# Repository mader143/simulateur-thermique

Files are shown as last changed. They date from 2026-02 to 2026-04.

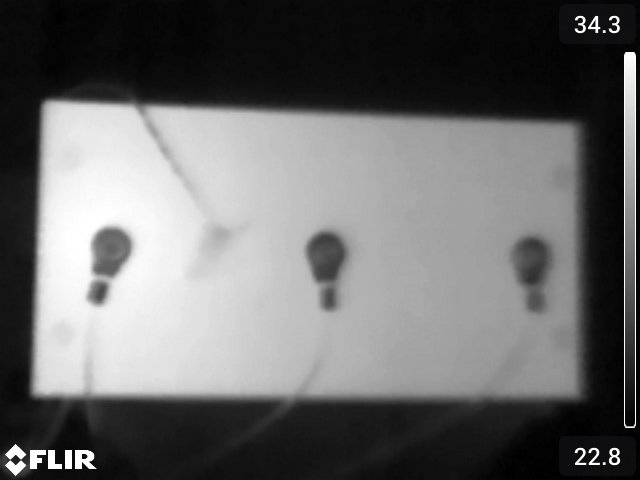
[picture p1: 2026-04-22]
PhotosThermiques_ValidationProto/FLIR0060.jpg

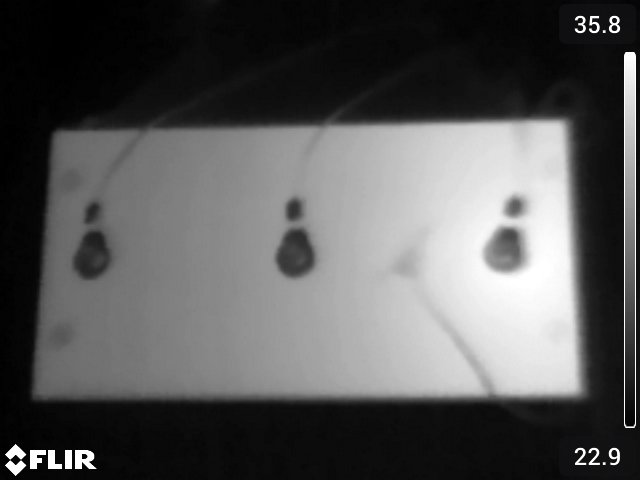
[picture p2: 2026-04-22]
PhotosThermiques_ValidationProto/FLIR0058.jpg

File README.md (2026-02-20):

# Simulateur Thermique
# Équipe 5 (Da best)

## Description

Simulateur thermique 2D pour modéliser la diffusion de chaleur dans une plaque métallique. Le projet regroupe une simulation numérique en Python avec interface graphique PyQt5, une simulation du système et du régulateur via Simulink (Matlab), du code Arduino pour l'acquisition et la régulation d'un prototype réel, et les données expérimentales pour la validation des différents paramètres identifiés.

## Contenu du projet

**Simulation Python** : Résolution par différences finies de l'équation de diffusion thermique, interface utilisateur interactive, génération de résultats et animations.

**Simulation Simulink** : Division du système/procédé en sous-systèmes et identification des fonctions de transfert de ceux-ci. Ajout d'un régulateur PID pour valider la commande contrôlant le prototype.

**Code Arduino** : Contrôleur PID pour régulation thermique, conditionnement des signaux, identification expérimentale, enregistrement des données.

**Conception PCB** : Schémas et circuits imprimés KiCad avec Arduino Mega 2560, amplificateurs opérationnels, et conditionnement analogique pour la lecture de la température en trois points sur la plaque métallique.

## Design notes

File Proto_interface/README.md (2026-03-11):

IMPORTANT **NE PAS CHANGER LES NOMS DES FICHIERS DANS Proto_Interface**

Pour pouvoir contrôler le Arduino par vscode :
1. Installer l'extension PlatformIO IDE
2. Appuyer sur la tête d'extraterrestre à gauche
3. Appuyer sur 'Project and configuration'
4. Dans 'simulateur-thermique\Proto_interface', appuyer sur 'Open'
5. Proto_interface ouvrira une seconde fois au même niveau que simulateur-thermique. C'est celui-là qui permet de rouler le code Arduino.

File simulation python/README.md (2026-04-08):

# Simulateur de diffusion de la chaleur

Simulation numérique 2D de la diffusion thermique dans une plaque rectangulaire avec interface graphique.

---

## Avant de commencer

Il faut avoir **Python 3.8 ou plus** installé sur l'ordinateur.

Ensuite, il faut installer les packages nécessaires en ouvrant un terminal et en collant cette commande :

```bash
pip install numpy numba PyQt5 pyqtgraph matplotlib
```

---

## Lancer le simulateur

S'assurer que tous les fichiers du projet sont dans le **même dossier**, puis exécuter :

```bash
python main.py
```

Mettre la fenêtre en plein écran pour voir tous les graphiques.

---

## Utilisation rapide

1. Cliquer sur **Charger les paramètres (json)** pour charger les valeurs par défaut.
2. Ajuster les paramètres ou les positions des thermistances si nécessaire.
3. Cliquer sur **Lancer la simulation** *(quelques secondes de délai normal au premier lancement)*.
4. Une fois terminé, choisir un dossier, entrer un nom de fichier, et cliquer sur **Sauvegarder les résultats**.

Voir le Manuel d'utilisation (.pdf) pour plus de détails.

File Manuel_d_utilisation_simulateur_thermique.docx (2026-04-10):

MANUEL D’UTILISATION - SIMULATEUR DE LA CHALEUR

1. Ouvrir le fichier nommé main.py et exécuter (run) le code.

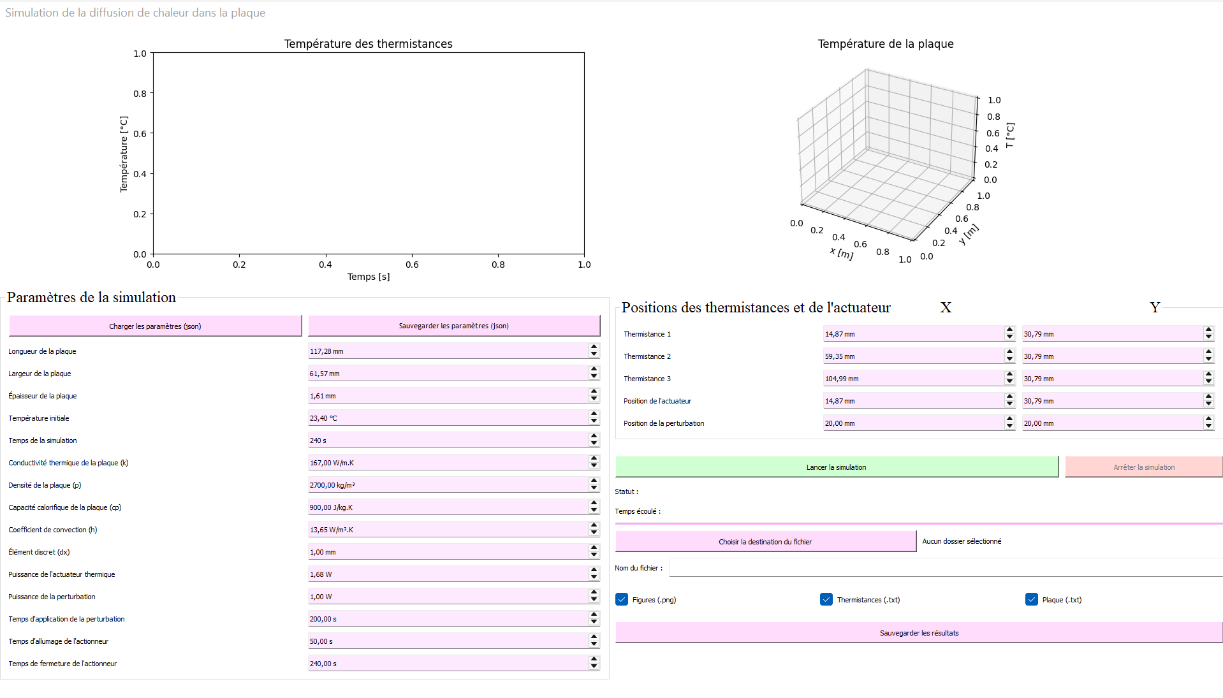
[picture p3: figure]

2. La fenêtre de l’interface s’ouvre. Mettre en grand écran pour voir tous les graphiques et fonctionnalités disponibles.
3. Pour débuter une simulation, choisir ou charger les paramètres de la simulation dans les champs de texte. Pour charger les paramètres par défaut contenus dans le fichier params_sim.json, il suffit de cliquer sur le bouton Charger les paramètres (json).
4. Il est également possible de modifier l’emplacement des thermistances, de l’actuateur et de la perturbation dans la section Position des thermistances et de l’actuateur.
5. Cliquer sur Lancer la simulation. Il est normal que cela prenne quelques secondes avant de démarrer lors de la première exécution de la simulation.
6. Une fois que le statut de la simulation est Simulation terminée, il est possible de sauvegarder les figures ainsi que les données utilisées pour les générer (.txt) en choisissant la destination sur l’ordinateur, en spécifiant le nom du fichier et en cliquant sur Sauvegarder les fichiers.

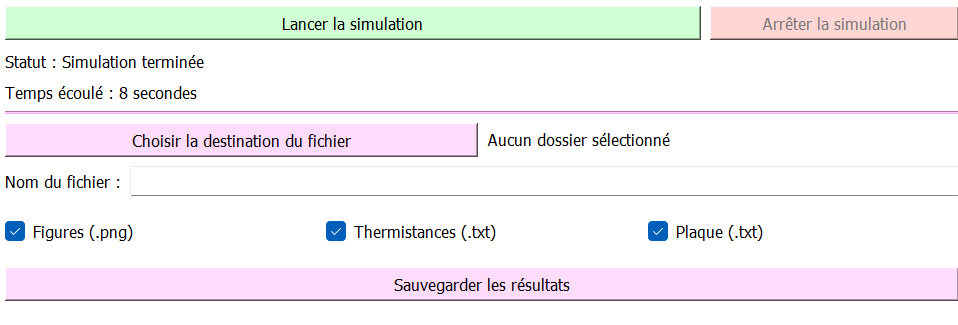
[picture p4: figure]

7. Le bouton Arrêter la simulation permet de arrêter la simulation. Il est également possible de sauvegarder les fichiers dans ce cas. Il n’est pas possible de continuer la simulation arrêter.

MANUEL D’UTILISATION - SIMULATEUR SIMULINK

1. Les fichiers nécessaires au bon fonctionnement du simulateur sont :
  a. simulink_08_04_procede.slx
  b. logique.m
  c. variables_simulation.m
  d. boucle_fermee.png
  e. boucle_ouverte.png
2. Une fois que le fichier simulink_08_04_procede.slx est ouvert, il faut run (exécuter) les fichiers logique.m et variables_simulation.m (à partir de la fenêtre classroom use).

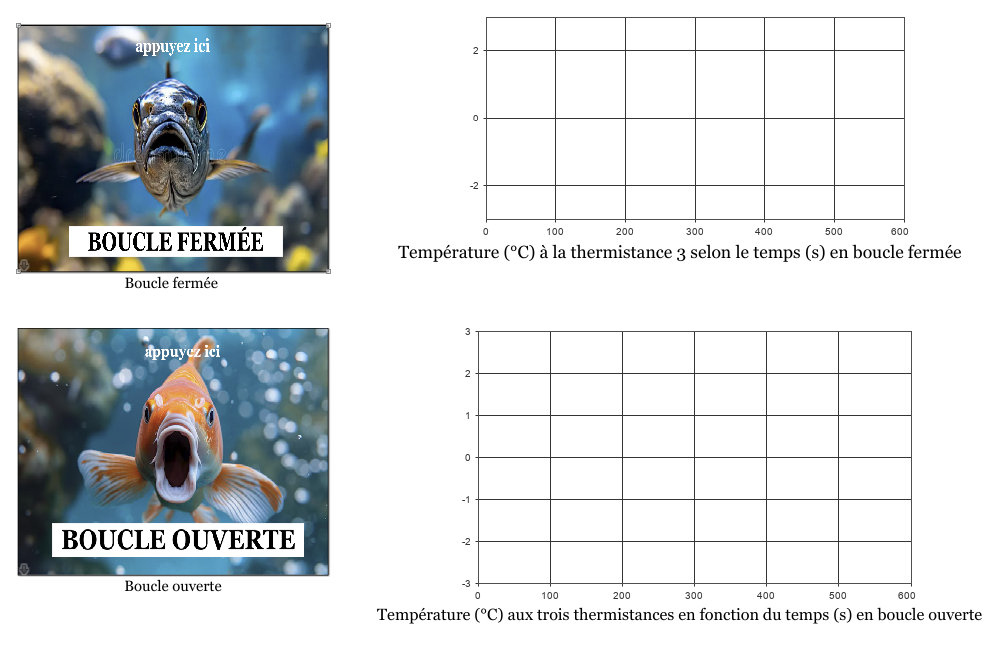
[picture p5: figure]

3. En cliquant sur l’autre fenêtre, l’interface s’affiche. Il est composé de 4 éléments : les paramètres de simulation en boucle ouverte et en boucle fermée et les graphiques affichant la réponse en boucle ouverte et en boucle fermée. Il ressemble à :

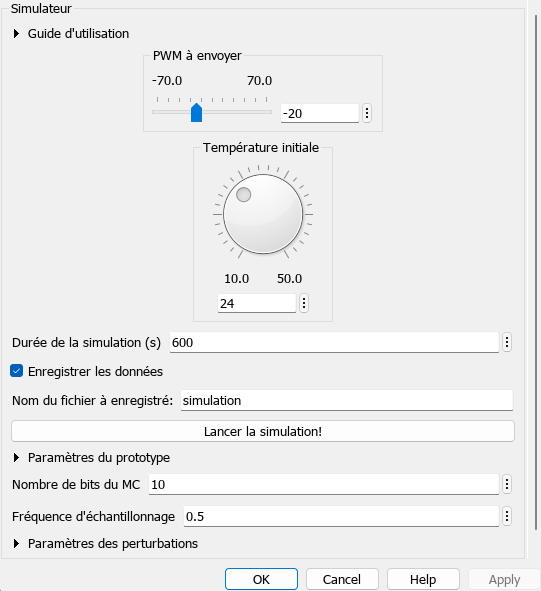
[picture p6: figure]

4. Pour la boucle ouverte, double cliquez sur le poisson ayant la bouche ouverte. Il est alors possible de spécifier l’échelon de commande voulu (PWM), la température initiale (°C), certains paramètres du prototype et les paramètres des perturbations.

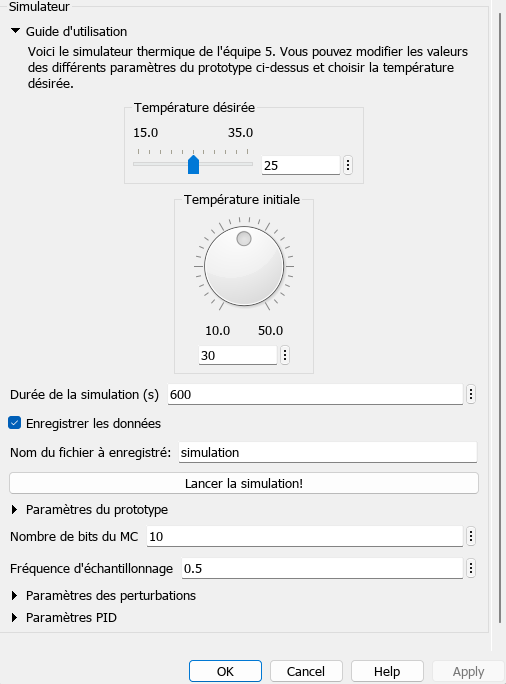
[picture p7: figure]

5. Pour la boucle fermée, de la même façon, choisir la température intitiale et désirée. D’autres paramètres modifiables sont aussi disponibles.
6. Les modifications des différentes fonctions de transfert et la visualisation des signaux se font directement dans la simulation (blocs et sous-systèmes). Cliquez sur la flèche dans le coin inférieur gauche de l’image correspondante à la boucle désirée pour y accéder.

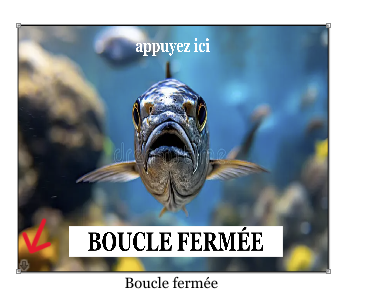
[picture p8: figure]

Exemple pour la boucle fermée :

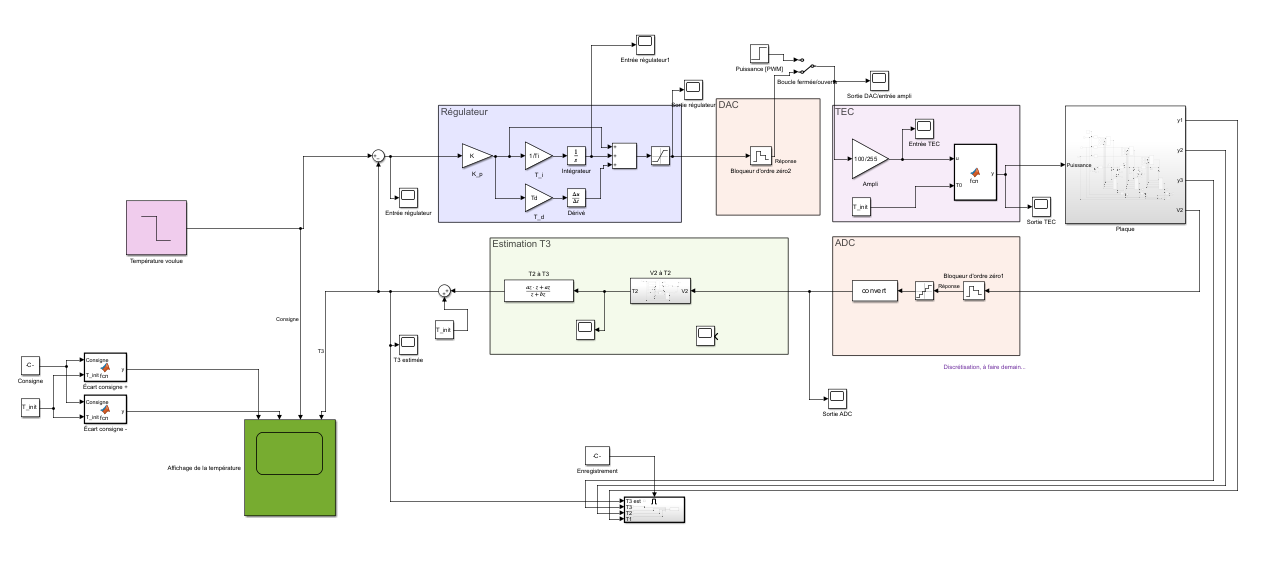
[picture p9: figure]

Équipe 05 GPH-2104 (H26)

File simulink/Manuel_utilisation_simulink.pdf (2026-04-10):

Équipe 05 | GPH-2104 (H26)
| MANUEL D’UTILISATION - SIMULATEUR SIMULINK

### 1. Les fichiers nécessaires au bon fonctionnement du simulateur sont :

a. simulink_08_04_procede.slx
b. logique.m
c. variables_simulation.m
d. boucle_fermee.png
e. boucle_ouverte.png
2. Une fois que le fichier simulink_08_04_procede.slx est ouvert, il faut run (exécuter) les fichiers logique.m et variables_simulation.m (à partir de la fenêtre classroom use).
3. En cliquant sur l’autre fenêtre, l’interface s’affiche. Il est composé de 4 éléments : les paramètres de simulation en boucle ouverte et en boucle fermée et les graphiques affichant la réponse en boucle ouverte et en boucle fermée. Il ressemble à :

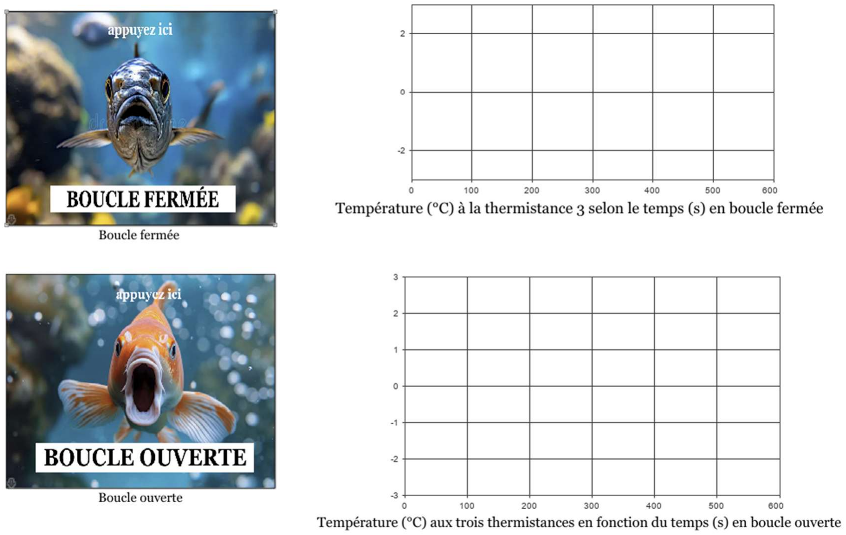
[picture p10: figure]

4. Pour la boucle ouverte, double cliquez sur le poisson ayant la bouche ouverte. Il est alors possible de spécifier l’échelon de commande voulu (PWM), la température initiale (°C), certains paramètres du prototype et les paramètres des perturbations.

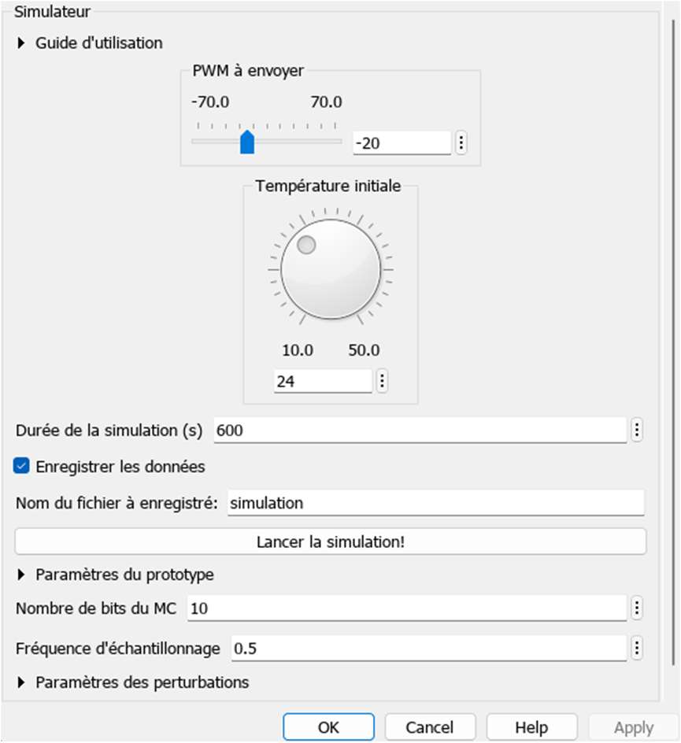
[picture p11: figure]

5. Pour la boucle fermée, de la même façon, choisir la température intitiale et désirée. D’autres paramètres modifiables sont aussi disponibles.

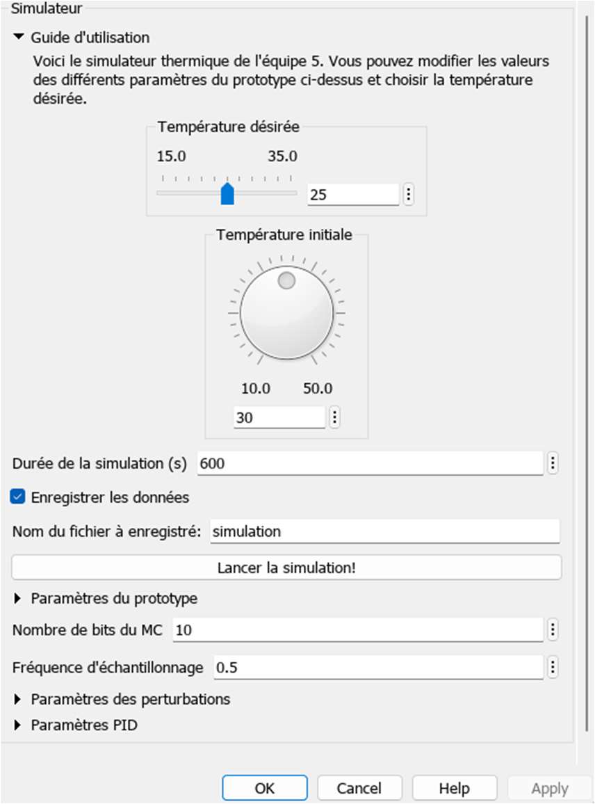
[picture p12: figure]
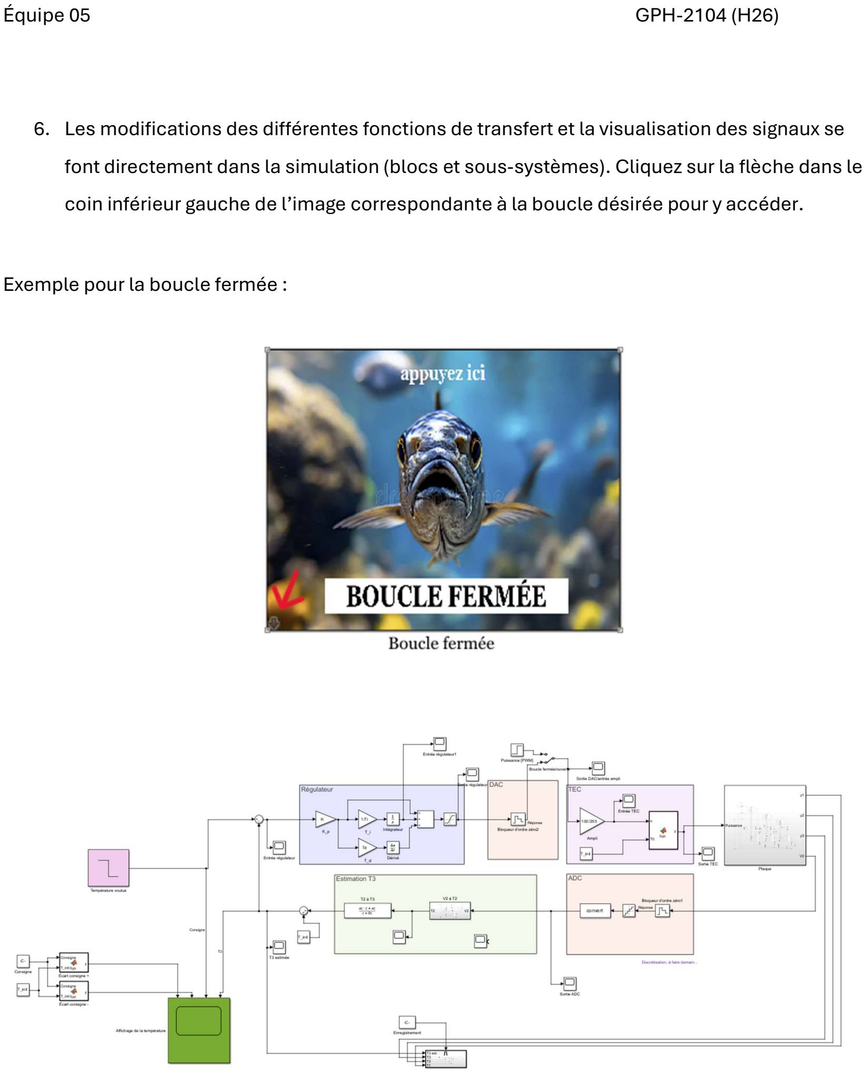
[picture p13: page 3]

6. Les modifications des différentes fonctions de transfert et la visualisation des signaux se font directement dans la simulation (blocs et sous-systèmes). Cliquez sur la flèche dans le coin inférieur gauche de l’image correspondante à la boucle désirée pour y accéder.

Exemple pour la boucle fermée :

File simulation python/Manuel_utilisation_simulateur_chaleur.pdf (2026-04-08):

Équipe 05 | GPH-2104 (H26)
| MANUEL D’UTILISATION - SIMULATEUR DE LA CHALEUR
1. Ouvrir le fichier nommé main.py et exécuter (run) le code.
2. La fenêtre de l’interface s’ouvre. Mettre en grand écran pour voir tous les graphiques et fonctionnalités disponibles.

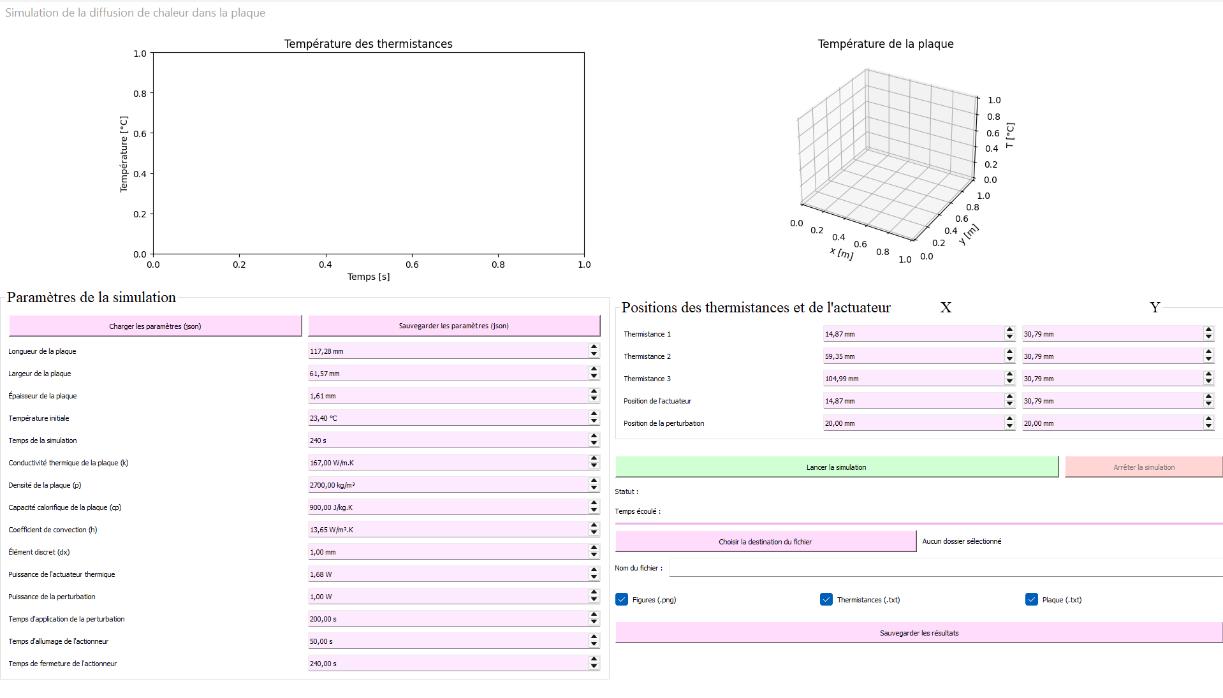
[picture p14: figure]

3. Pour débuter une simulation, choisir ou charger les paramètres de la simulation dans les champs de texte. Pour charger les paramètres par défaut contenus dans le fichier params_sim.json, il suffit de cliquer sur le bouton Charger les paramètres (json).

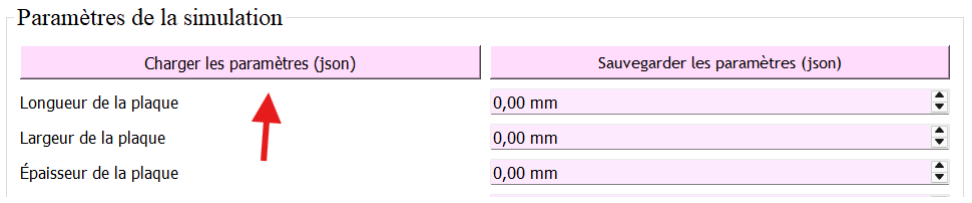
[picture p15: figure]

4. Il est également possible de modifier l’emplacement des thermistances, de l’actuateur et de la perturbation dans la section Position des thermistances et de l’actuateur.
5. Cliquer sur Lancer la simulation. Il est normal que cela prenne quelques secondes avant de démarrer lors de la première exécution de la simulation.

Équipe 05 | GPH-2104 (H26)
6. Une fois que le statut de la simulation est Simulation terminée, il est possible de sauvegarder les figures ainsi que les données utilisées pour les générer (.txt) en choisissant la destination sur l’ordinateur, en spécifiant le nom du fichier et en cliquant sur Sauvegarder les fichiers.

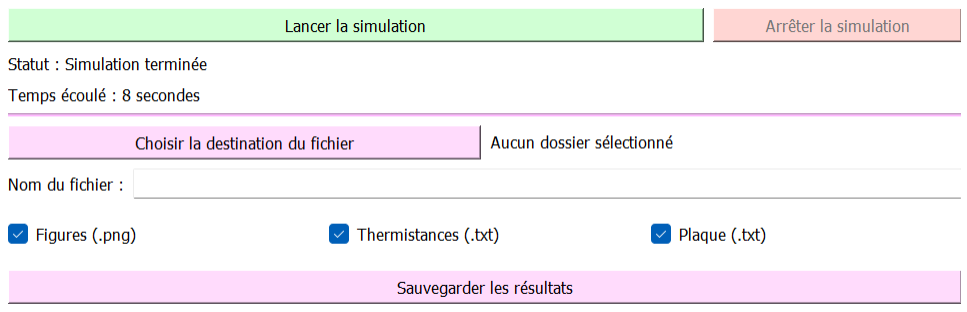
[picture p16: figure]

7. Le bouton Arrêter la simulation permet de arrêter la simulation. Il est également possible de sauvegarder les fichiers dans ce cas. Il n’est pas possible de continuer la simulation arrêter.

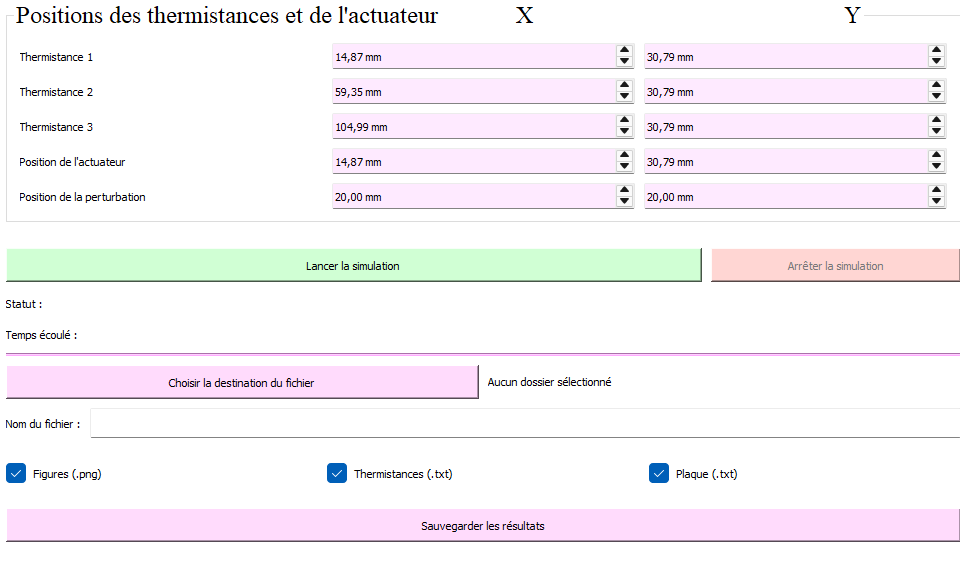
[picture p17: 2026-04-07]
simulation python/Screenshot rapport/Interface_simul_python_position_therm.png

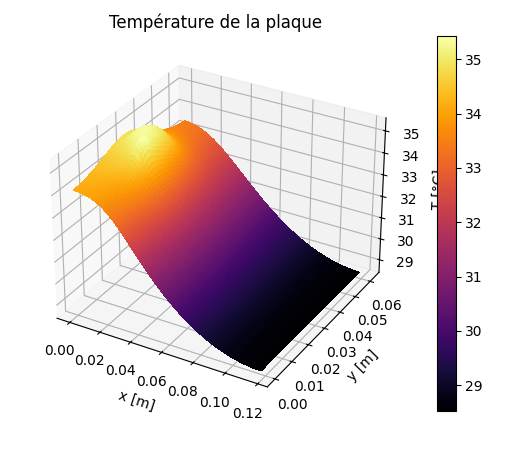
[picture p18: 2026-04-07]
simulation python/Screenshot rapport/Interface_simul_python_plaque.png

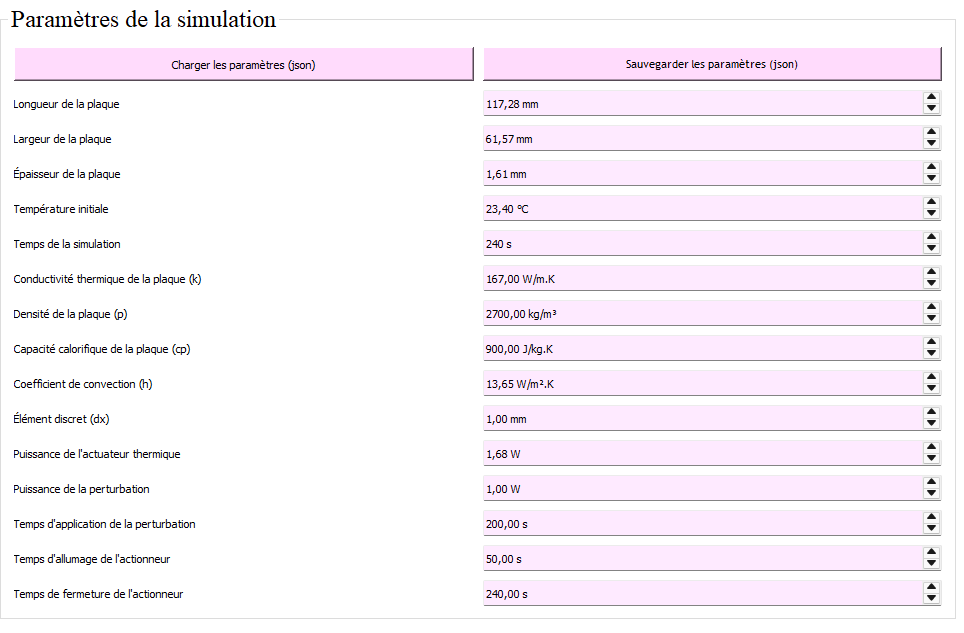
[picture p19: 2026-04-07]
simulation python/Screenshot rapport/Interface_simul_python_parametres.png

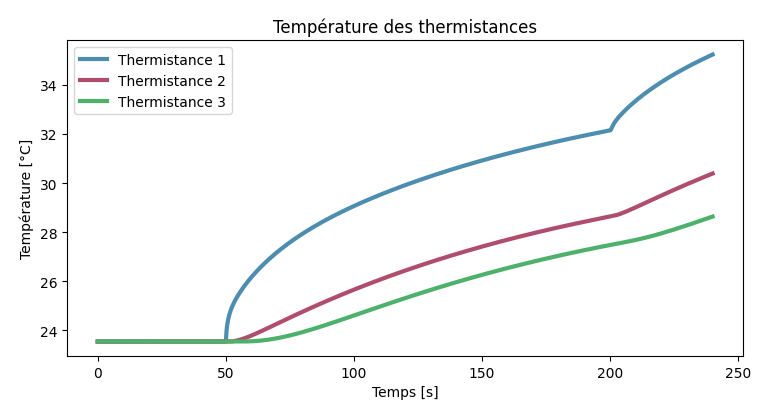
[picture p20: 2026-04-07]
simulation python/Screenshot rapport/Interface_simul_python_graphique_temps.png

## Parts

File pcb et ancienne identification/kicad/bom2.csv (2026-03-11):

Id | Référence | Empreinte | Quantité | Désignation | Fournisseur et réf
1 | RV3,RV2,RV4,RV1 | trimpot | 4 | R_Potentiometer_Trim
2 | J1 | MTA_CONN2_640445-2 | 1 | MTA_02
3 | R6,R4,R11,R1 | Resistance SMT | 4 | 10K
4 | R3,R10,R14,R9,R5,R19,R7,R12 | Resistance SMT | 8 | 5.6K
5 | C1,C4,C2,C3 | condensateur 1uF | 4 | 1 μF
6 | TH3,TH2,TH4,TH1 | MTA_CONN2_640445-2 | 4 | Screw_Terminal_01x02
7 | D1 | LED_D5.0mm | 1 | LED
8 | U1,U3,U2,U4 | LMC6482_SMT | 4 | LMC6482IMX_NOPB
9 | R8,R2,R13,R15 | Resistance SMT | 4 | 3.3K
10 | R18 | Resistance SMT | 1 | 560
11 | J2 | MTA_CONN4_640445-4 | 1 | MTA_04
12 | power2,analogA0-A7,comm1,analogA8-A15,pwm2 | PinHeader_1x08_P2.54mm_Vertical | 5 | Conn_01x08_Pin
13 | pwm1 | PinHeader_1x10_P2.54mm_Vertical | 1 | Conn_01x10_Pin

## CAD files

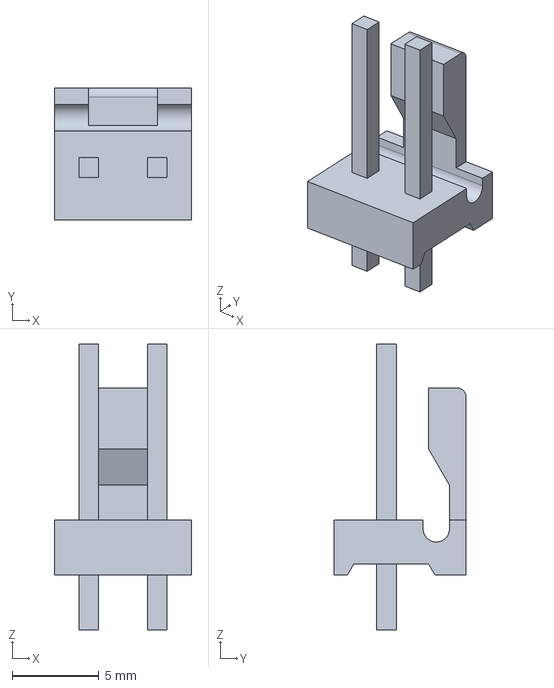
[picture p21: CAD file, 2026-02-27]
pcb et ancienne identification/kicad/CON_02_MTA_MALE_MATHILDE/c-640445-2-al-3d.stp
7.92 x 7.62 x 16.5 mm

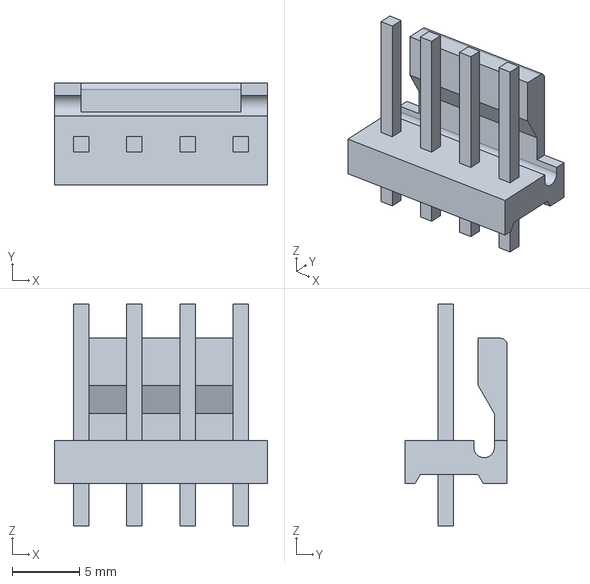
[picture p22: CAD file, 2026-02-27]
pcb et ancienne identification/kicad/CON_04_MTA_MALE_MATHILDE/c-640445-4-al-3d.stp
15.8 x 7.62 x 16.5 mm

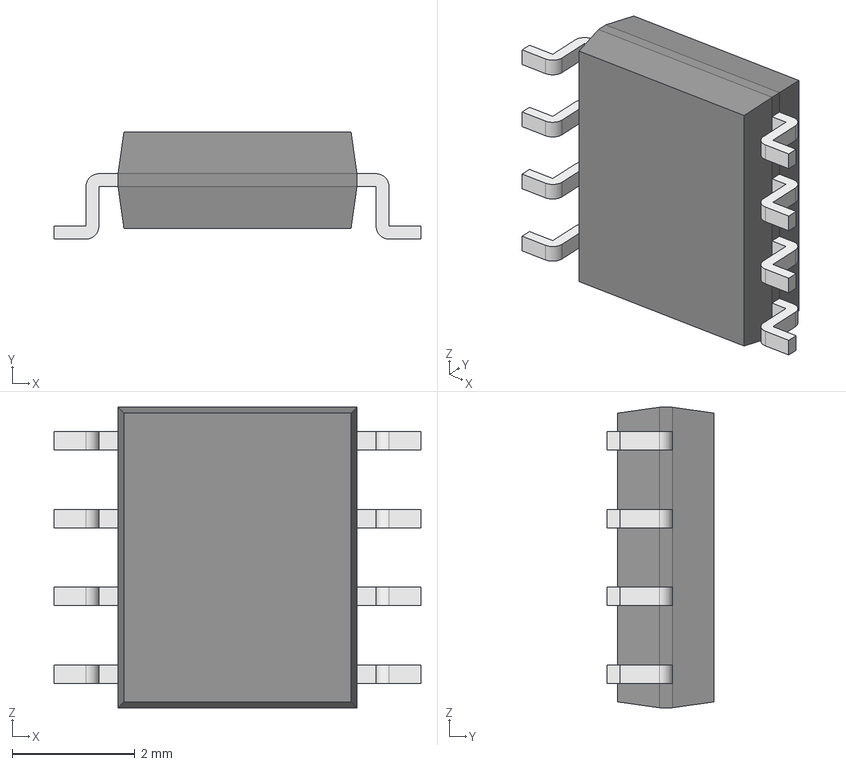
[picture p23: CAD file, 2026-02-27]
pcb et ancienne identification/kicad/LMC6482_SMT_MATHILDE/LMC6482IMX_NOPB.step
5.99 x 1.75 x 4.91 mm
Body001 (Mirror #1) x 4
XY-plane x 12
X-axis x 12

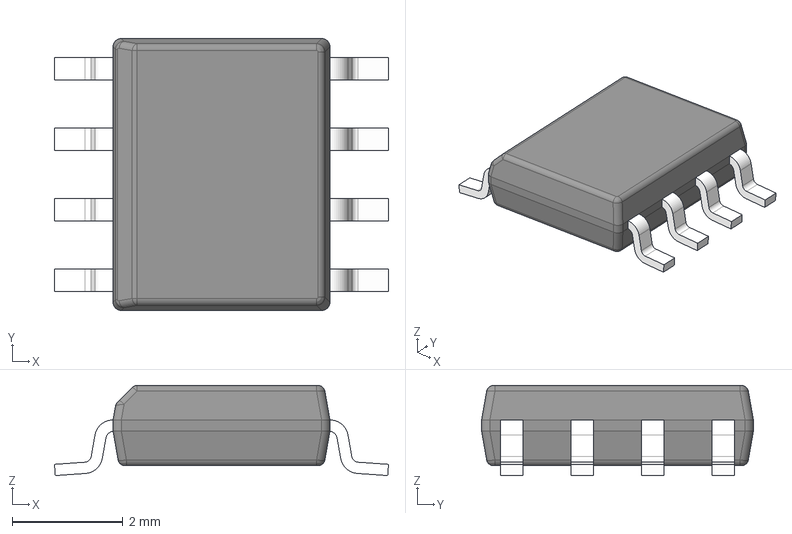
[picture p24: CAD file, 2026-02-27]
pcb et ancienne identification/kicad/LMC6482_SMT_MATHILDE/D0008A.stp
6.02 x 4.90 x 1.63 mm
BODY-SO
LEAD-D0008A x 8

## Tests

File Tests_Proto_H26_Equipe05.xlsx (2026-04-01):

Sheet: Plan de Test
Déroulement général
 | Un membre de l'équipe enseignante démarre l'exécution du plan de test, il effectue les tests de convivialité et note les résultats dans son propre fichier excel
 | Le test sans perturbation est ensuite démarré. Au bout d'une minute ou deux, le membre de l'équipe enseignante prend en photo les courbes affichées, en prenant soin d'avoir le numéro de l'équipe dans la photo.
 | Le membre de l'équipe enseignante peut alors quitter
 | L'équipe complète le test selon les directives ci-bas et sauve les données pour remplir l'onglet "Réponse à l'échelon"
 | Lorsque prête pour le test de perturbation, l'équipe lève la main
 | Un membre de l'équipe enseignante démarre le test, lorsque la perturbation est allumée, il prend les courbes affichées en photo, avec le numéro d'équipe et peut quitter
 | L'équipe complète le test selon les directives ci-bas et sauve les données pour remplir l'onglet "Réponse perturbation"
 | Lorsque prête pour le test de robutesse, l'équipe lève la main
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

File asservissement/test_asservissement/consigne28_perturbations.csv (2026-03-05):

temps_s | temperature_C | erreur | commande_u
0.000 | 23.17 | 4.83 | 42.34
0.500 | 23.17 | 4.83 | 43.16
1.000 | 23.23 | 4.77 | 43.43
1.500 | 23.30 | 4.70 | 43.68
2.000 | 23.36 | 4.64 | 43.93
2.500 | 23.36 | 4.64 | 44.72
3.000 | 23.42 | 4.58 | 44.96
3.500 | 23.48 | 4.52 | 45.18
4.000 | 23.48 | 4.52 | 45.95
4.500 | 23.55 | 4.45 | 46.17
5.000 | 23.55 | 4.45 | 46.93
5.500 | 23.67 | 4.33 | 46.58
6.000 | 23.74 | 4.26 | 46.77
6.500 | 23.80 | 4.20 | 46.94
7.000 | 23.86 | 4.14 | 47.10
7.500 | 23.92 | 4.08 | 47.26
8.000 | 23.99 | 4.01 | 47.40
8.500 | 24.05 | 3.95 | 47.53
9.000 | 24.11 | 3.89 | 47.66
9.500 | 24.24 | 3.76 | 47.22
10.000 | 24.30 | 3.70 | 47.31
10.500 | 24.43 | 3.57 | 46.85
11.000 | 24.49 | 3.51 | 46.91
11.500 | 24.61 | 3.39 | 46.41
12.000 | 24.74 | 3.26 | 45.89
12.500 | 24.86 | 3.14 | 45.35
13.000 | 24.92 | 3.08 | 45.34
13.500 | 25.05 | 2.95 | 44.77
14.001 | 25.17 | 2.83 | 44.18
14.501 | 25.30 | 2.70 | 43.57
15.001 | 25.42 | 2.58 | 42.94
15.501 | 25.55 | 2.45 | 42.29
16.001 | 25.67 | 2.33 | 41.62
16.501 | 25.73 | 2.27 | 41.47
17.001 | 25.92 | 2.08 | 40.23
17.501 | 26.04 | 1.96 | 39.50
18.001 | 26.17 | 1.83 | 38.75
18.501 | 26.29 | 1.71 | 37.97
19.001 | 26.41 | 1.59 | 37.18
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

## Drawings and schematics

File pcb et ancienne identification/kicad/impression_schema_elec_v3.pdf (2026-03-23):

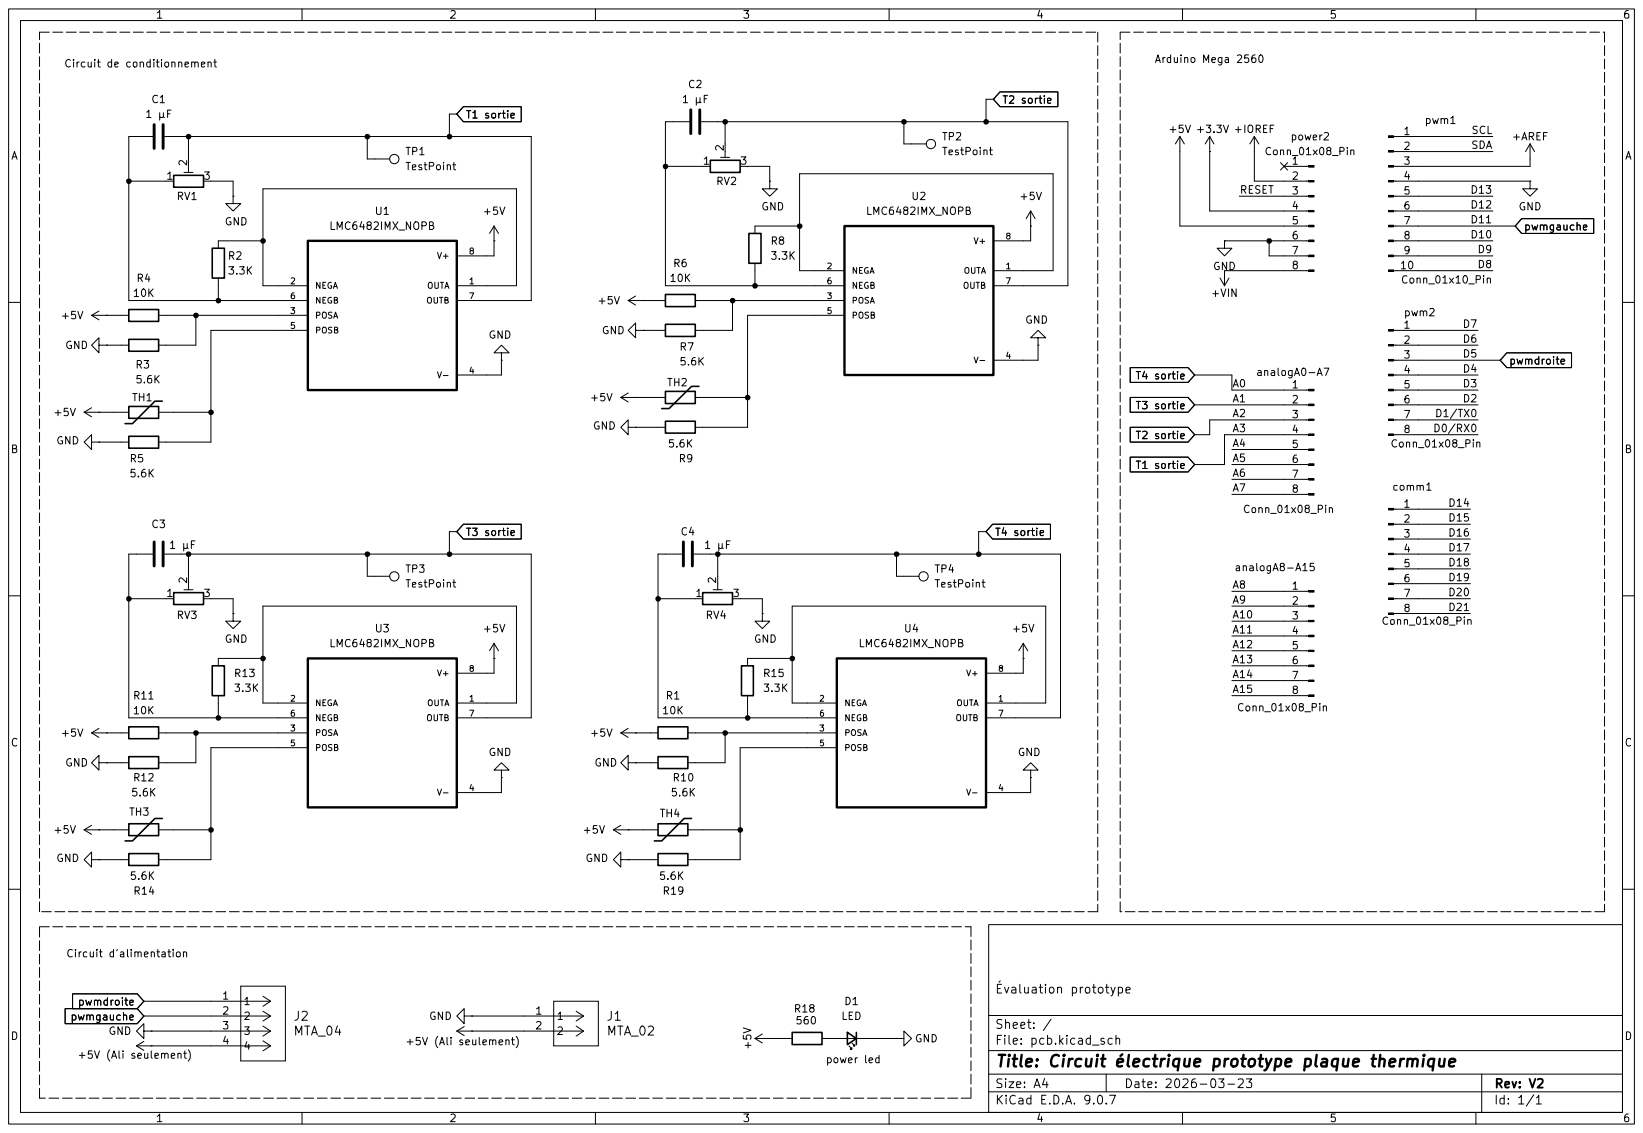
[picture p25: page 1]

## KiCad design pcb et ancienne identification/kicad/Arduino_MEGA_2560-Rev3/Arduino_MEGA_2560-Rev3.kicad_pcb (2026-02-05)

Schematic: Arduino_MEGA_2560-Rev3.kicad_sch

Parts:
ADCH31: 8x1F-H8.5; SMARTPRJ_1X08
ADCL31: 8x1F-H8.5; SMARTPRJ_1X08
C1, C14, C15: 22p; SMARTPRJ_C0603-ROUND
C2, C3, C4, C5, C6, C7, C8, C9, C11, C12: 100n; SMARTPRJ_C0603-ROUND
C10, C13: 1u; SMARTPRJ_C0603-ROUND
COMMUNICATION31: 8x1F-H8.5; SMARTPRJ_1X08
D1: M7; DIODE_SMB
D2, D3: CD1206-S01575; DIODE_MINIMELF
F1: MF-MSMF050-2 500mA; RCL_L1812
FD1, FD2, FD3, FD4: FIDUCIALMOUNT; SMARTPRJ_FIDUCIA-MOUNT
GROUND31: JUMPER_SJ
IC1: NCP1117ST50T3G; LINEAR_SOT223
IC3: ATMEGA2560-16AU; SMARTPRJ_TQFP100
IC4: ATMEGA16U2-MU; SMARTPRJ_MLF32
IC6: LP2985-33DBVR; SMARTPRJ_SOT23-DBV
IC7: LMV358IDGKR; LINEAR_MSOP08
ICSP1_31: 3x2M; SMARTPRJ_2X03
ICSP_31: 3x2M; SMARTPRJ_2X03
JP5: 2x2M - NM; SMARTPRJ_2X02
JP6: 10x1F-H8.5; SMARTPRJ_1X10
L1: BLM21; WUERTH-ELEKTRONIK_0805
L31: YELLOW; LED_CHIP-LED0805
ON31: GREEN; LED_CHIP-LED0805
PC1, PC2: 47u; RCL_PANASONIC_D
POWER31: 8x1F-H8.5; SMARTPRJ_1X08
PWML31: 8x1F-H8.5; SMARTPRJ_1X08
R1, R2: 1M; SMARTPRJ_R0603-ROUND
RESET31: TS42031-160R-TR-7260; SMARTPRJ_TS42
RESET-EN31: JUMPER_SJ
RN1, RN5: 10K; RESISTOR-DIL_CAT16
RN2: 22R; RESISTOR-DIL_CAY16
RN3, RN4: 1k; RESISTOR-DIL_CAY16
RX31: YELLOW; LED_CHIP-LED0805
T1: FDN340P; ZETEX_SOT-23
TX31: YELLOW; LED_CHIP-LED0805
U$1: DISCLAIMER; SMARTPRJ_DISCLAIMER
X1: POWERSUPPLY_DC21MMX; SMARTPRJ_POWERSUPPLY_DC-21MM
X2: USB-B_TH; SMARTPRJ_PN61729
XIO31: 18x2F-H8.5; SMARTPRJ_2X18
Y1: CSTCE16M0V53-R0 16MHZ; SMARTPRJ_RESONATOR
Y2: 16MHz; SMARTPRJ_QS
Z1, Z2: CG0603MLC-05E; VARISTOR_CT_CN0603

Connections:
+3V3: C13.2, IC6.5 (OUT), IC7.6 (-IN), POWER31.4
+5V: C4.1, C5.1, C6.1, C9.1, C11.2, D2.C, D3.C, IC1.2 (OUT), IC1.4 (OUT), IC3.10 (VCC), IC3.31 (VCC1), IC3.61 (VCC2), IC3.80 (VCC3), IC3.100 (AVCC), IC4.4 (VCC), IC4.32 (AVCC), IC6.1 (IN), IC6.3 (ON/~OFF), IC7.8 (V+), ICSP1_31.2, ICSP_31.2, PC2.+, POWER31.2, POWER31.5, RN1.6 (2), RN1.7 (2), RN3.1, RN4.5 (2), RN4.6 (2), RN5.2 (1), RN5.8 (2), T1.2 (S), XIO31.1, XIO31.2
/8PB4: IC4.18 ((T1/PCINT4)PB4), JP5.1
/8PB5: IC4.19 ((PCINT5)PB5), JP5.3
/8PB6: IC4.20 ((PCINT6)PB6), JP5.2
/8PB7: IC4.21 ((PCINT7/OC0A/OC1C)PB7), JP5.4
/ADC0: ADCL31.1, IC3.97 ((ADC0)PF0)
/ADC1: ADCL31.2, IC3.96 ((ADC1)PF1)
/ADC2: ADCL31.3, IC3.95 ((ADC2)PF2)
/ADC3: ADCL31.4, IC3.94 ((ADC3)PF3)
/ADC4: ADCL31.5, IC3.93 ((ADC4/TCK)PF4)
/ADC5: ADCL31.6, IC3.92 ((ADC5/TMS)PF5)
/ADC6: ADCL31.7, IC3.91 ((ADC6/TDO)PF6)
/ADC7: ADCL31.8, IC3.90 ((ADC7/TDI)PF7)
/ADC8: ADCH31.1, IC3.89 (PK0(ADC8/PCINT16))
/ADC9: ADCH31.2, IC3.88 (PK1(ADC9/PCINT17))
/ADC10: ADCH31.3, IC3.87 (PK2(ADC10/PCINT18))
/ADC11: ADCH31.4, IC3.86 (PK3(ADC11/PCINT19))
/ADC12: ADCH31.5, IC3.85 (PK4(ADC12/PCINT20))
/ADC13: ADCH31.6, IC3.84 (PK5(ADC13/PCINT21))
/ADC14: ADCH31.7, IC3.83 (PK6(ADC14/PCINT22))
/ADC15: ADCH31.8, IC3.82 (PK7(ADC15/PCINT23))
/AREF: C3.1, IC3.98 (AREF), JP6.3
/CMP: C12.2, IC7.5 (+IN), RN5.3 (1), RN5.5 (2)
/D+: RN2.5 (2), X2.3, Z2.2
/D-: RN2.8 (2), X2.2, Z1.2
/DTR: C7.1, IC4.13 ((CTS/HWB/AIN6/TO/INT7)PD7), RN3.4 (1)
/GATE_CMD: IC7.7 (OUT), T1.3 (G)
/L13: IC7.1 (OUT), IC7.2 (-IN), RN3.7 (2)
/M8RXD: IC4.9 ((TXD1/INT3)PD3), RN4.7 (2)
/M8TXD: IC4.8 ((RXD1/AIN1/INT2)PD2), RN4.8 (2)
/MISO2: IC4.17 ((PD0/MISO/PCINT3)PB3), ICSP1_31.1
/MOSI2: IC4.16 ((PDI/MOSI/PCINT2)PB2), ICSP1_31.4
/N$2: L31.A, RN3.2 (1)
/N$3: ON31.A, RN3.8 (2)
/N$54: RN4.4 (1), RX31.A
/N$55: RN4.3 (1), TX31.A
/PA0: IC3.78 ((AD0)PA0), XIO31.3
/PA1: IC3.77 ((AD1)PA1), XIO31.4
/PA2: IC3.76 ((AD2)PA2), XIO31.5
/PA3: IC3.75 ((AD3)PA3), XIO31.6
/PA4: IC3.74 ((AD4)PA4), XIO31.7
/PA5: IC3.73 ((AD5)PA5), XIO31.8
/PA6: IC3.72 ((AD6)PA6), XIO31.9
/PA7: IC3.71 ((AD7)PA7), XIO31.10
/PB0: IC3.19 ((SS/PCINT0)PB0), XIO31.34
/PB1: IC3.20 ((SCK/PCINT1)PB1), ICSP_31.3, XIO31.33
/PB2: IC3.21 ((MOSI/PCINT2)PB2), ICSP_31.4, XIO31.32
/PB3: IC3.22 ((MISO/PCINT3)PB3), ICSP_31.1, XIO31.31
/PB4: IC3.23 ((OC2A/PCINT4)PB4), JP6.8
/PB5: IC3.24 ((OC1A/PCINT5)PB5), JP6.7
/PB6: IC3.25 ((OC1B/PCINT6)PB6), JP6.6
/PB7: IC3.26 ((OC0A/OC1C/PCINT7)PB7), IC7.3 (+IN), JP6.5
/PC0: IC3.53 ((A8)PC0), XIO31.18
/PC1: IC3.54 ((A9)PC1), XIO31.17
/PC2: IC3.55 ((A10)PC2), XIO31.16
/PC3: IC3.56 ((A11)PC3), XIO31.15
/PC4: IC3.57 ((A12)PC4), XIO31.14
/PC5: IC3.58 ((A13)PC5), XIO31.13
/PC6: IC3.59 ((A14)PC6), XIO31.12
/PC7: IC3.60 ((A15)PC7), XIO31.11
/PD7: IC3.50 ((T0)PD7), XIO31.19
/PE0: IC3.2 ((RXD0/PCIN8)PE0), PWML31.1, RN4.2 (1)
/PE1: IC3.3 ((TXD0)PE1), PWML31.2, RN4.1
/PE3: IC3.5 ((OC3A/AIN1)PE3), PWML31.6
/PE4: IC3.6 ((OC3B/INT4)PE4), PWML31.3
/PE5: IC3.7 ((OC3C/INT5)PE5), PWML31.4
/PG0: IC3.51 ((WR)PG0), XIO31.22
/PG1: IC3.52 ((RD)PG1), XIO31.21
/PG2: IC3.70 ((ALE)PG2), XIO31.20
/PG5: IC3.1 ((OC0B)PG5), PWML31.5
/PH3: IC3.15 (PH3(OC4A)), PWML31.7
/PH4: IC3.16 (PH4(OC4B)), PWML31.8
/PH5: IC3.17 (PH5(OC4C)), JP6.10
/PH6: IC3.18 (PH6(OC2B)), JP6.9
/PL0: IC3.35 (PL0(ICP4)), XIO31.30
/PL1: IC3.36 (PL1(ICP5)), XIO31.29
/PL2: IC3.37 (PL2(T5)), XIO31.28
/PL3: IC3.38 (PL3(OC5A)), XIO31.27
/PL4: IC3.39 (PL4(OC5B)), XIO31.26
/PL5: IC3.40 (PL5(OC5C)), XIO31.25
/PL6: IC3.41 (PL6), XIO31.24
/PL7: IC3.42 (PL7), XIO31.23
/PWRIN: D1.A, X1.2
/RD+: IC4.29 (D+), RN2.4 (1)
/RD-: IC4.30 (D-), RN2.1
/RESET: C1.1, C7.2, D3.A, IC3.30 (RESET), ICSP_31.5, POWER31.3, RESET31.3, RESET31.4, RESET-EN31.1, RESET-EN31.2, RN5.1
/RESET2: D2.A, IC4.24 (RESET(PC1/DW)), ICSP1_31.5, RN5.7 (2)
/RXD1: COMMUNICATION31.3, IC3.45 ((RXD1/INT2)PD2)
/RXD2: COMMUNICATION31.5, IC3.12 (PH0(RXD2))
/RXD3: COMMUNICATION31.7, IC3.63 (PJ0(RXD3/PCINT9))
/RXL: IC4.10 ((INT5/AIN3)PD4), RX31.C
/SCK2: IC4.15 ((SCLK/PCINT1)PB1), ICSP1_31.3
/SCL: COMMUNICATION31.1, IC3.43 ((SCL/INT0)PD0), JP6.1, RN1.2 (1)
/SDA: COMMUNICATION31.2, IC3.44 ((SDA/INT1)PD1), JP6.2, RN1.3 (1)
/TXD1: COMMUNICATION31.4, IC3.46 ((TXD1/INT3)PD3)
/TXD2: COMMUNICATION31.6, IC3.13 (PH1(TXD2))
/TXD3: COMMUNICATION31.8, IC3.64 (PJ1(TXD3/PCINT10))
/TXL: IC4.11 ((XCK/AIN4/PCINT12)PD5), TX31.C
/UGND: C10.2, GROUND31.1, IC4.28 (UGND), L1.1, X2.4
/USBVCC: C8.1, F1.1, IC4.31 (UVCC), T1.1 (D)
/USHIELD: L1.2, X2.P$1, X2.P$2, Z1.1, Z2.1
/VIN: C2.1, D1.C, IC1.3 (IN), PC1.+, POWER31.8, RN5.6 (2)
/VUCAP: C10.1, IC4.27 (UCAP)
/XT1: C14.1, IC4.1 (XTAL1), R2.1, Y2.2
/XT2: C15.1, IC4.2 (XTAL2(PC0)), R2.2, Y2.1
/XTAL1: IC3.34 (XTAL1), R1.1, Y1.3
/XTAL2: IC3.33 (XTAL2), R1.2, Y1.1
/XVCC: F1.2, X2.1
GND: C1.2, C2.2, C3.2, C4.2, C5.2, C6.2, C8.2, C9.2, C11.1, C12.1, C13.1, C14.2, C15.2, GROUND31.2, IC1.1 (GND/ADJ), IC3.11 (GND), IC3.32 (GND1), IC3.62 (GND2), IC3.81 (GND3), IC3.99 (AGND), IC4.3 (GND), IC4.33 (PAD), IC6.2 (GND), IC7.4 (V-), ICSP1_31.6, ICSP_31.6, JP6.4, L31.C, ON31.C, PC1.-, PC2.-, POWER31.6, POWER31.7, RESET31.1, RESET31.2, RN3.5 (2), RN5.4 (1), X1.1, X1.3, XIO31.35, XIO31.36, Y1.2

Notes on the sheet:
(SCK)
pwm
USB boot En
(MOSI)
Arduino MEGA 2560
(MISO)
(TX0)
(RX0)
(SS)

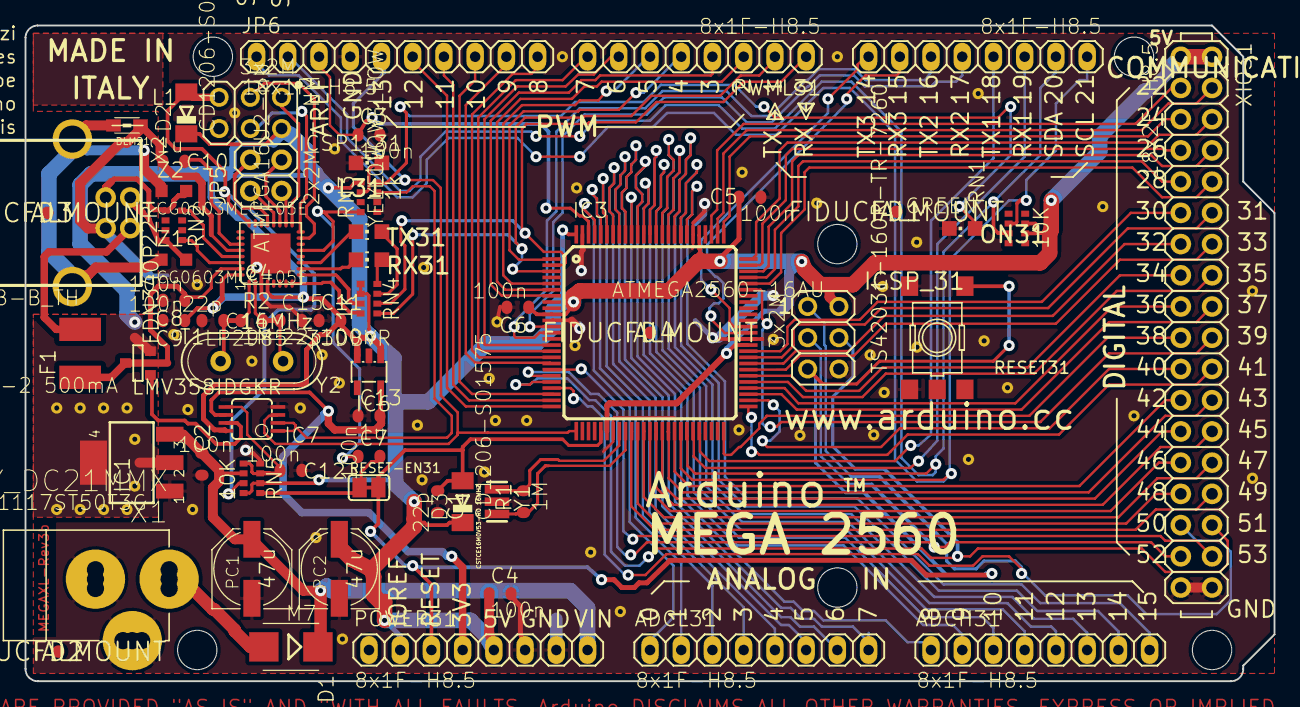
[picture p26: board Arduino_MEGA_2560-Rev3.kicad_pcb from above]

Board: 2 copper layers, 101.6 x 53.3 mm, 69 parts (1 on the bottom side), 110 nets.

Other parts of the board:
@HOLE0, @HOLE1, @HOLE2, @HOLE3, @HOLE4, @HOLE5: (no value)

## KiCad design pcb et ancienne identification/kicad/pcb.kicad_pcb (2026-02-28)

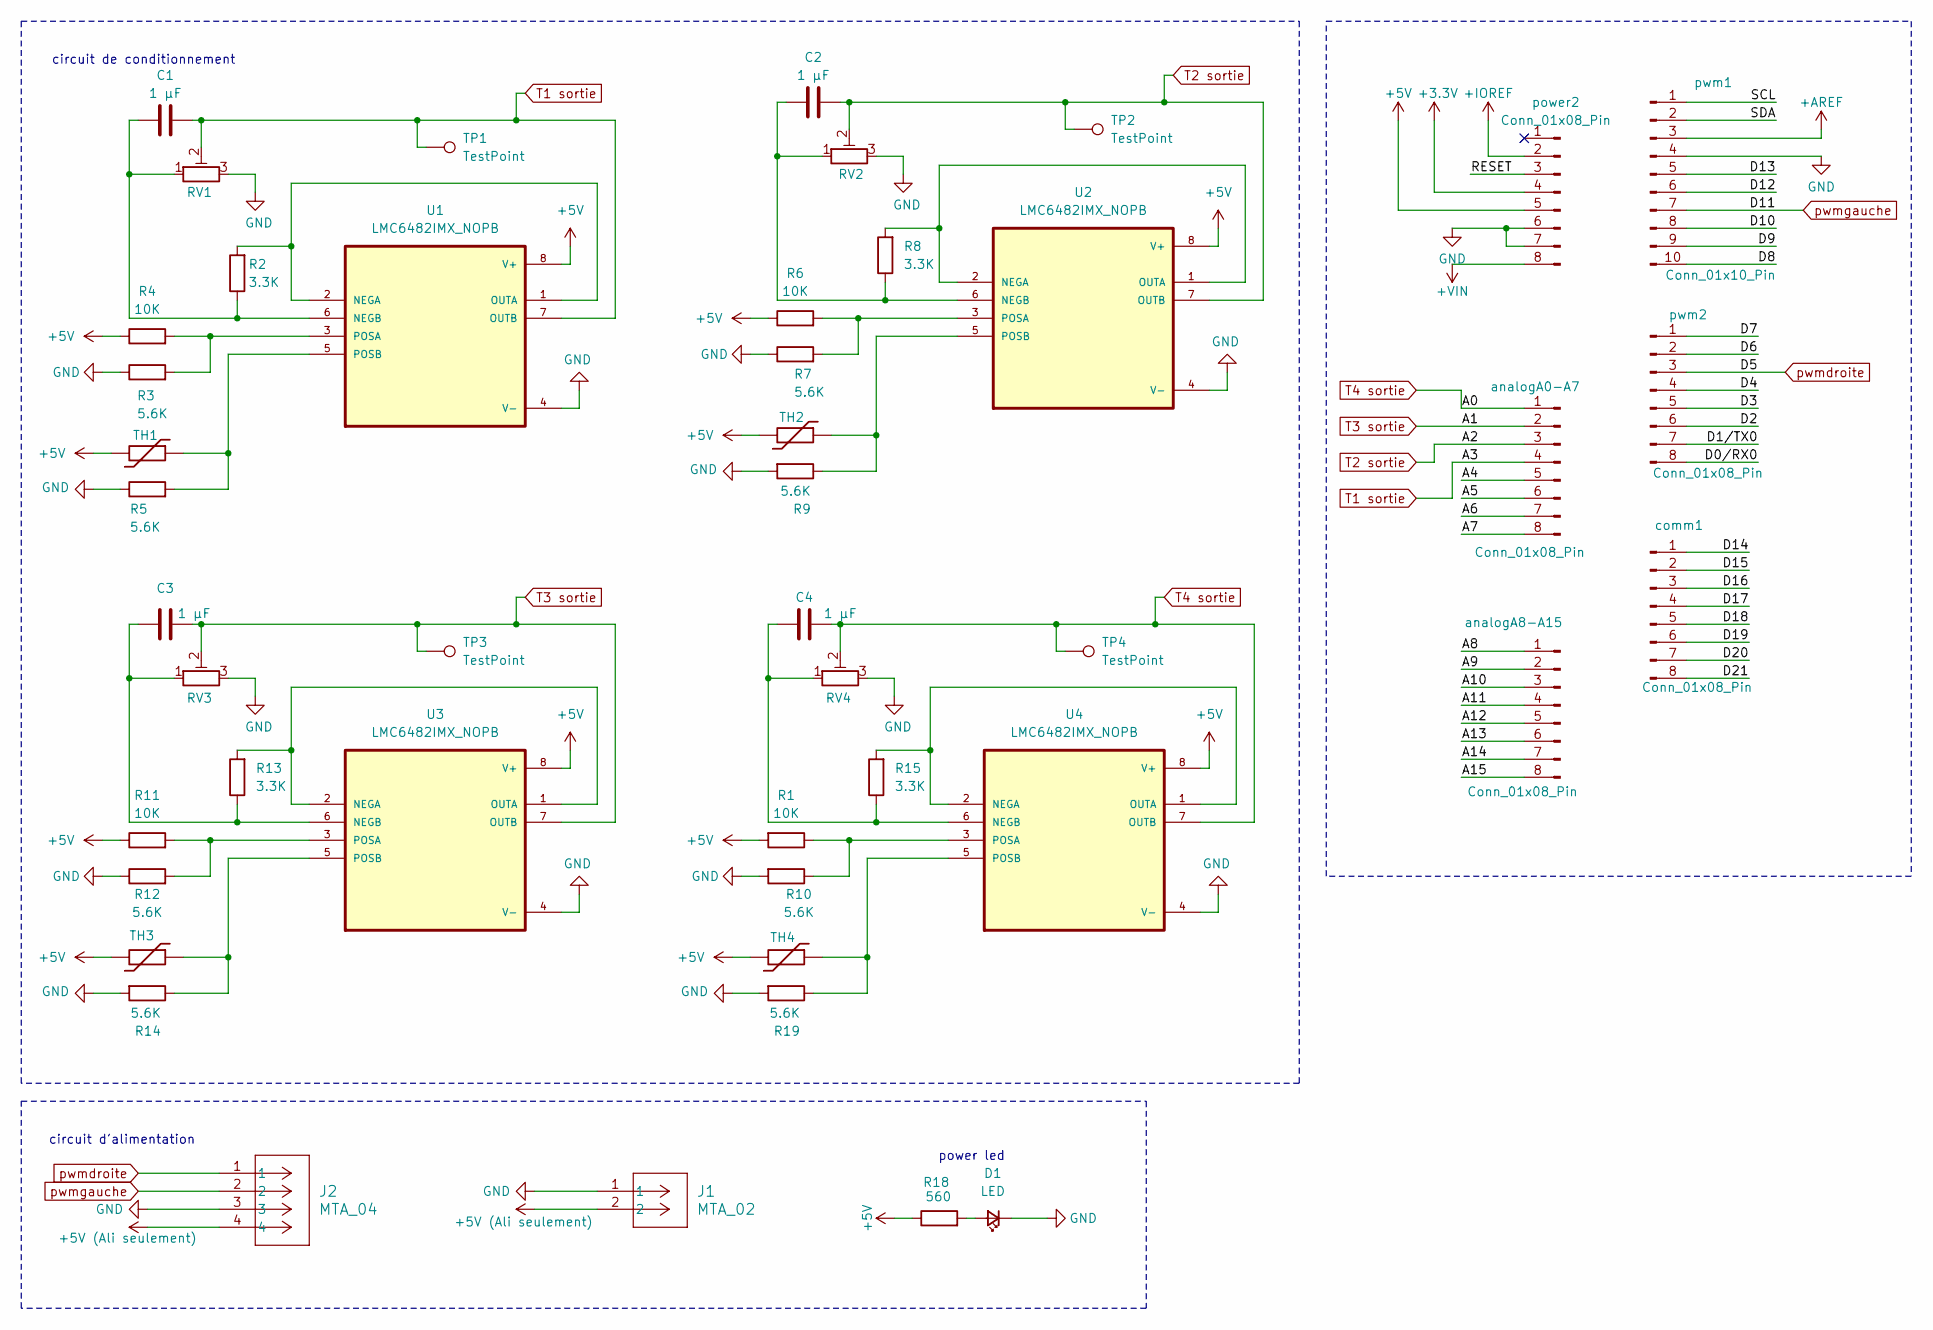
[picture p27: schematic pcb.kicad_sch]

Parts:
C1, C2, C3, C4: 1 μF; condensateur 1uF
D1: LED; LED_D5.0mm
J1: MTA_02; MTA_CONN2_640445-2
J2: MTA_04; MTA_CONN4_640445-4
R1, R4, R6, R11: 10K; Resistance SMT
R2, R8, R13, R15: 3.3K; Resistance SMT
R3, R5, R7, R9, R10, R12, R14, R19: 5.6K; Resistance SMT
R18: 560; Resistance SMT
RV1, RV2, RV3, RV4: R_Potentiometer_Trim; trimpot
TH1, TH2, TH3, TH4: Screw_Terminal_01x02; MTA_CONN2_640445-2
TP1, TP2, TP3, TP4: TestPoint; TestPoint_THTPad_D1.5mm_Drill0.7mm
U1, U2, U3, U4: LMC6482IMX_NOPB; LMC6482_SMT
analogA0-A7, analogA8-A15: Conn_01x08_Pin; PinHeader_1x08_P2.54mm_Vertical
comm1: Conn_01x08_Pin; PinHeader_1x08_P2.54mm_Vertical
power2: Conn_01x08_Pin; PinHeader_1x08_P2.54mm_Vertical
pwm1: Conn_01x10_Pin; PinHeader_1x10_P2.54mm_Vertical
pwm2: Conn_01x08_Pin; PinHeader_1x08_P2.54mm_Vertical

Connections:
+3.3V: power2.4
+5V: R1.2, R4.1, R6.1, R11.1, R18.1, TH1.2, TH2.2, TH3.2, TH4.2, U1.8 (V+), U2.8 (V+), U3.8 (V+), U4.8 (V+), power2.5
+5V (Ali seulement): J1.2, J2.4
+AREF: pwm1.3
+IOREF: power2.2
+VIN: power2.8
/A4: analogA0-A7.5
/A5: analogA0-A7.6
/A6: analogA0-A7.7
/A7: analogA0-A7.8
/A8: analogA8-A15.1
/A9: analogA8-A15.2
/A10: analogA8-A15.3
/A11: analogA8-A15.4
/A12: analogA8-A15.5
/A13: analogA8-A15.6
/A14: analogA8-A15.7
/A15: analogA8-A15.8
/D0/RX0: pwm2.8
/D1/TX0: pwm2.7
/D2: pwm2.6
/D3: pwm2.5
/D4: pwm2.4
/D6: pwm2.2
/D7: pwm2.1
/D8: pwm1.10
/D9: pwm1.9
/D10: pwm1.8
/D12: pwm1.6
/D13: pwm1.5
/D14: comm1.1
/D15: comm1.2
/D16: comm1.3
/D17: comm1.4
/D18: comm1.5
/D19: comm1.6
/D20: comm1.7
/D21: comm1.8
/RESET: power2.3
/SCL: pwm1.1
/SDA: pwm1.2
GND: D1.1 (K), J1.1, J2.3, R3.1, R5.1, R7.1, R9.2, R10.2, R12.1, R14.2, R19.2, RV1.3, RV2.3, RV3.3, RV4.3, U1.4 (V-), U2.4 (V-), U3.4 (V-), U4.4 (V-), power2.6, power2.7, pwm1.4
unnamed: D1.2 (A), R18.2
unnamed: R2.2, U1.1 (OUTA), U1.2 (NEGA)
unnamed: C1.1, R2.1, RV1.1, U1.6 (NEGB)
unnamed: R3.2, R4.2, U1.3 (POSA)
unnamed: R5.2, TH1.1, U1.5 (POSB)
unnamed: R8.2, U2.1 (OUTA), U2.2 (NEGA)
unnamed: C2.1, R8.1, RV2.1, U2.6 (NEGB)
unnamed: R6.2, R7.2, U2.3 (POSA)
unnamed: R9.1, TH2.1, U2.5 (POSB)
unnamed: R13.2, U3.1 (OUTA), U3.2 (NEGA)
unnamed: C3.1, R13.1, RV3.1, U3.6 (NEGB)
unnamed: R11.2, R12.2, U3.3 (POSA)
unnamed: R14.1, TH3.1, U3.5 (POSB)
unnamed: R15.2, U4.1 (OUTA), U4.2 (NEGA)
unnamed: C4.1, R15.1, RV4.1, U4.6 (NEGB)
unnamed: R1.1, R10.1, U4.3 (POSA)
unnamed: R19.1, TH4.1, U4.5 (POSB)
T1 sortie: C1.2, RV1.2, TP1.1, U1.7 (OUTB), analogA0-A7.4
T2 sortie: C2.2, RV2.2, TP2.1, U2.7 (OUTB), analogA0-A7.3
T3 sortie: C3.2, RV3.2, TP3.1, U3.7 (OUTB), analogA0-A7.2
T4 sortie: C4.2, RV4.2, TP4.1, U4.7 (OUTB), analogA0-A7.1
pwmdroite: J2.1, pwm2.3
pwmgauche: J2.2, pwm1.7

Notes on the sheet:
circuit d'alimentation
power led
circuit de conditionnement

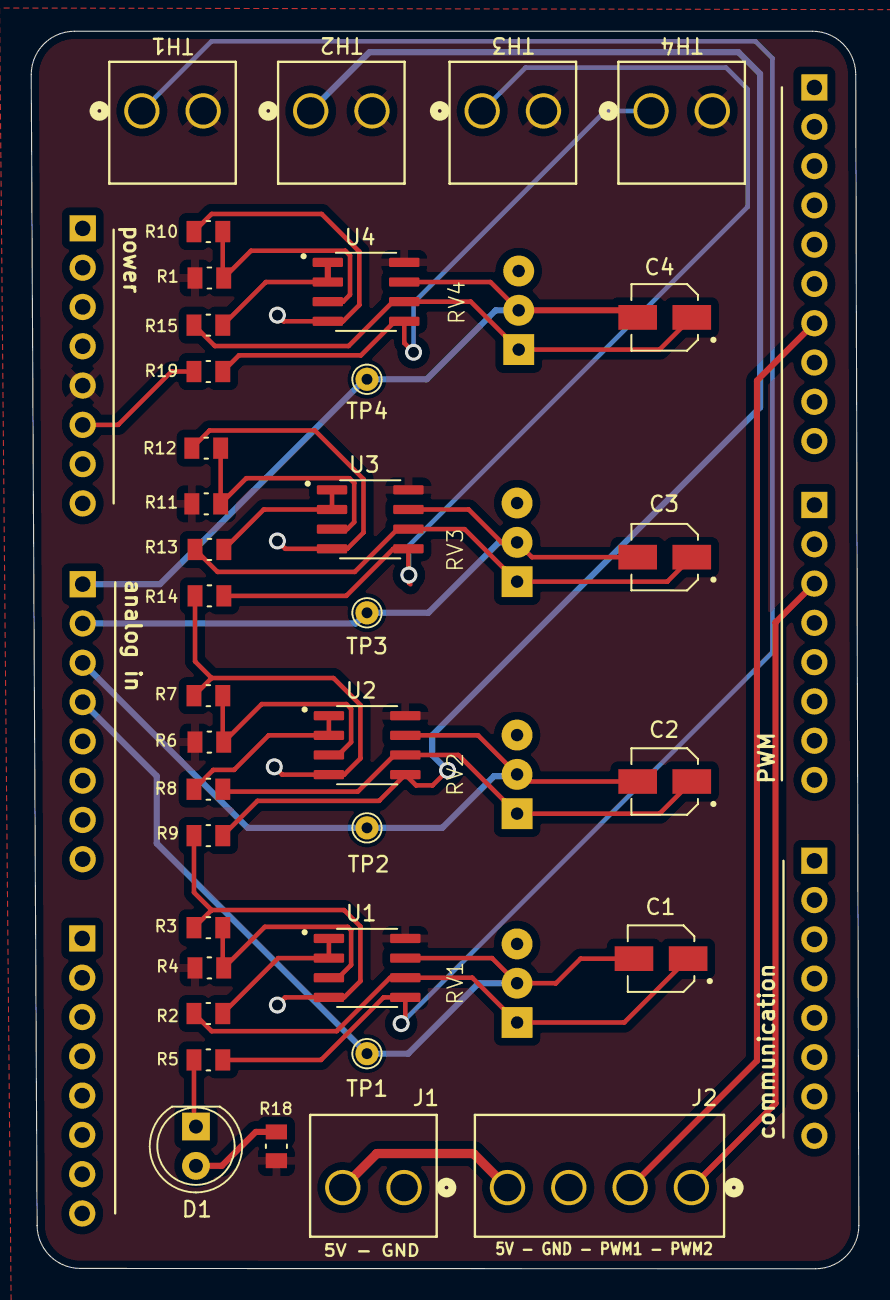
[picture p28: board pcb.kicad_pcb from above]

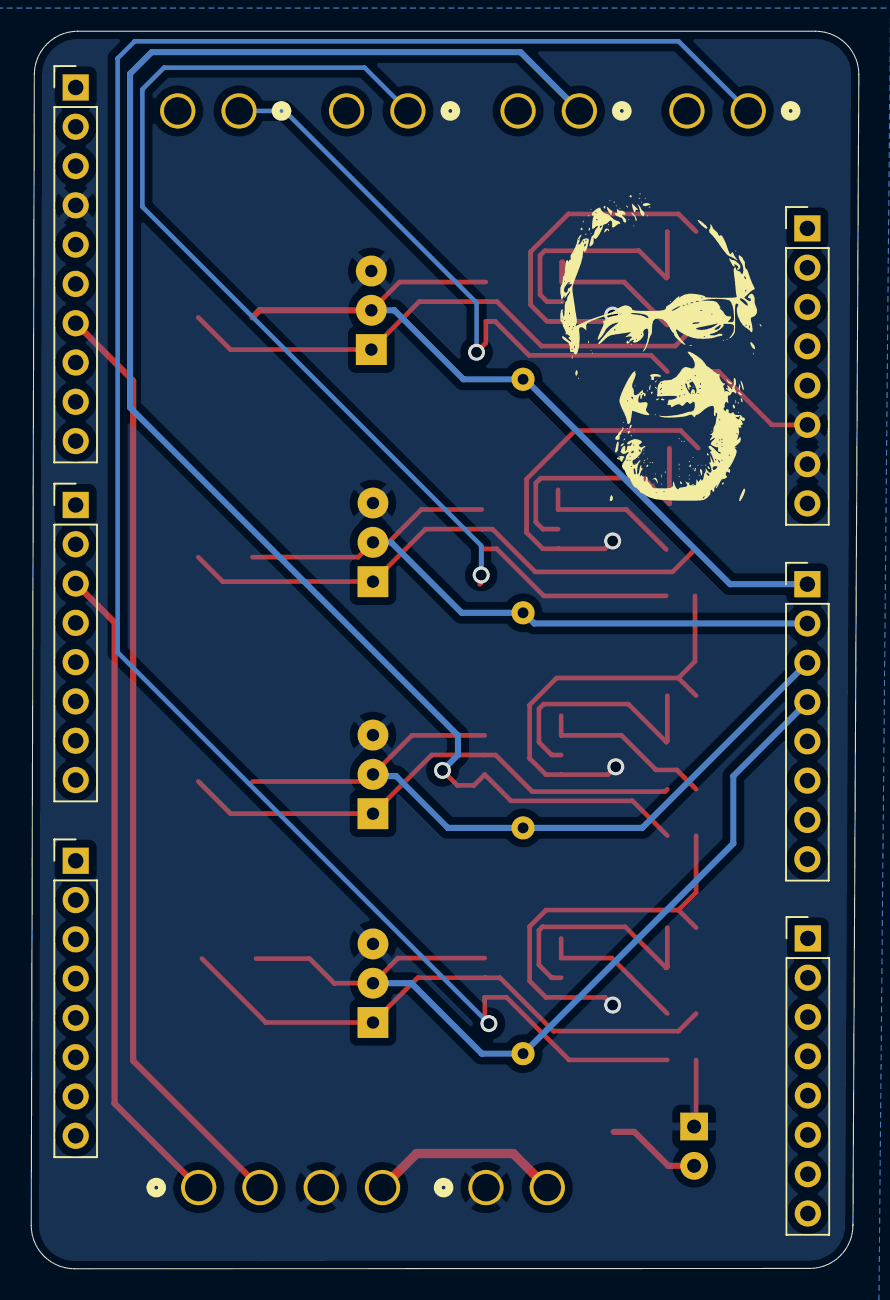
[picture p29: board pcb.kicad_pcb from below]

Board: 2 copper layers, 53.5 x 80.0 mm, 46 parts (6 on the bottom side), 26 nets.

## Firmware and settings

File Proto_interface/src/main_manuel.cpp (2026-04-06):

#include <Arduino.h>
// Code updaté qui détermine si on prend le PID chaud ou froid
// ===================== PWM =====================
const int pwmPin_CHAUD = 5;
const int pwmPin_FROID = 11;
int pwm_manuel = 0;

// ===================== PID DISCRET =====================
float setpoint = 20;

const float T_s = 0.5;

float K  = 10.85;
float Ti = 271.0;
float Td = 0.0;
float new_K  = 0.0;
float new_Ti = 0.0;
float new_Td = 0.0;


// ===================== THERMISTANCES =====================
#define RT0 10000
const float T0 = 25.0 + 273.15;

struct Thermistance {
  int   pin;
  float Rf;
  float Rg;
  float R1;
  float V1;
  float V2;
  float B;
};

Thermistance therm[3] = {
  {A3, 3300, 5600, 3300, 1.774, 5.0, 4010},
  {A2, 6300, 5600, 3300, 1.80,  5.0, 3984},
  {A1, 6300, 5600, 3300, 1.79,  5.0, 3700},
};

// ===================== ESTIMATEUR T3 depuis T1 =====================
const float G1_b0 =  0.002432;
const float G1_b1 =  0.002432;
const float G1_a1 = -0.9926;

float T1_init = 0.0;
float u1_prev = 0.0;
float y1_prev = 0.0;

// ===================== ESTIMATEUR T3 depuis T2 =====================
const float G2_b0 =  0.009158;
const float G2_b1 =  0.009158;
const float G2_a1 = -0.98;

float T2_init = 0.0;
float u2_prev = 0.0;
float y2_prev = 0.0;

float T3_init = 0.0;

// ===================== VARIABLES PID =====================
float e[3]   = {0.0, 0.0, 0.0};
float u_prev = 0.0;

const float U_MAX =  255.0;
const float U_MIN = -255.0;

// ===================== CSV / LOG =====================
const unsigned long DUREE_ENREGISTREMENT = 1000;
unsigned long tempsDebut;
bool modeCSV = true;

// ===================== TIMING =====================
unsigned long lastPID = 0;


// =====================================================
// FONCTION MESURE TEMPÉRATURE
// =====================================================
float mesureTemperature(Thermistance t) {
  float Vout = (5.0 / 1023.0) * analogRead(t.pin);
  float RT = ((t.Rf + t.R1) * t.Rg * t.V2) /
             (t.R1 * Vout + t.Rf * t.V1) - t.Rg;
  float TX = 1.0 / ((log(RT / RT0) / t.B) + (1.0 / T0));
  return TX - 273.15;
}

float mesureTemperature1(Thermistance t) {
  float Vout = (5.0 / 1023.0) * analogRead(t.pin);
  float TX = 9.1562*Vout + 7.9337;
  return TX;
}


// =====================================================
// ENVOI PWM CHAUD / FROID
// =====================================================
void envoyerPWM(float u) {
  u = constrain(u, U_MIN, U_MAX);
  if (u > 0) {
    analogWrite(pwmPin_CHAUD, (int) u);
    analogWrite(pwmPin_FROID, 0);
  } else {
    analogWrite(pwmPin_CHAUD, 0);
    analogWrite(pwmPin_FROID, (int)(-u));
  }
}


// =====================================================
// SETUP
// =====================================================
void setup() {
  Serial.begin(9600);

  pinMode(pwmPin_CHAUD, OUTPUT);
  pinMode(pwmPin_FROID, OUTPUT);
  analogWrite(pwmPin_CHAUD, 0);
  analogWrite(pwmPin_FROID, 0);

  delay(2000);

  T1_init = mesureTemperature1(therm[0]);
  T2_init = mesureTemperature(therm[1]);
  T3_init = mesureTemperature(therm[2]);

  u1_prev = 0.0;  y1_prev = 0.0;
  u2_prev = 0.0;  y2_prev = 0.0;

  Serial.println("temps_s,T1_C,T2_C,T3_C,T3_estimT2,T3_estimT1,T3_moy,erreur,commande_u");
  tempsDebut = millis();
}


// =====================================================
// LOOP
// =====================================================
void loop() {
  unsigned long now = millis();


  if (Serial.available() > 0) {
    String cmd = Serial.readStringUntil('\n');
    cmd.trim();

    if (cmd.startsWith("CONFIG_MANUELLE:")){
      String valeurs = cmd.substring(16);
      pwm_manuel  = valeurs.substring(0).toInt();
      Serial.print("ON ENVOIE CE PWM :");
      Serial.println(pwm_manuel);
    }

    if (cmd.startsWith("CONFIG:")) {
      String valeurs = cmd.substring(7);
      pwm_manuel = 0;
      Serial.println(valeurs);
      int v1 = valeurs.indexOf(',');
      int v2 = valeurs.indexOf(',', v1 + 1);
      int v3 = valeurs.indexOf(',', v2 + 1);
      int v4 = valeurs.indexOf(',', v3 + 1);
      int v5 = valeurs.indexOf(',', v4 + 1);
      int v6 = valeurs.indexOf(',', v5 + 1);
      Serial.println(v1);
      Serial.println(v2);
      Serial.println(v3);
      Serial.println(v4);
      Serial.println(v5);
      Serial.println(v6);

      // Réinitialisation des valeurs stockées quand on applique une nouvelle consigne
      u_prev = 0.0;
      e[1] = 0.0;
      e[2] = 0.0;

      if (v1 > 0 && v2 > v1 + 1 && v3 > v2 + 1) {
        float new_sp = valeurs.substring(0, v1).toFloat();
        if (new_sp > 23.5) {
            Serial.println("on est dans la boucle plus grande");
            new_K  = valeurs.substring(v1 + 1, v2).toFloat();
            new_Ti = valeurs.substring(v2 + 1, v3).toFloat();
            new_Td = valeurs.substring(v3 + 1, v4).toFloat();
            Serial.println(new_K);

        } else {
            Serial.println("On refroidit");
            new_K  = valeurs.substring(v4 + 1, v5).toFloat();
            new_Ti = valeurs.substring(v5 + 1, v6).toFloat();
            new_Td = valeurs.substring(v6 + 1).toFloat();
        }
        Serial.println("NOUVELLE VALEURS DE K, T_I ET T_D");
        Serial.println(new_K, 3);
        Serial.println(new_Ti, 3);
        Serial.println(new_Td, 3);


        if (new_Ti != 0.0) {
          setpoint = new_sp;
          K        = new_K;
          Ti       = new_Ti;
          Td       = new_Td;

          Serial.println("ACK:CONFIG_COMPLETE");
        } else {
          Serial.println("ERR:Ti_INVALIDE");
        }
      } else {
        Serial.println("ERR:FORMAT_INVALIDE");
      }
    }
  }

  if (now - lastPID >= (unsigned long)(T_s * 1000)) {
    lastPID = now;
    float T1 = mesureTemperature1(therm[0]);
    float T2 = mesureTemperature(therm[1]);
    float T3 = mesureTemperature(therm[2]);
    double t_s = (now - tempsDebut) / 1000.0;
    float T3_estimT1 = T3;
    float T3_estimT2 = T3;
    float T3_moy = T3;
    float u_sat = 0;
    float Vout1 = (5.0 / 1023.0) * analogRead(therm[0].pin);
    float Vout2 = (5.0 / 1023.0) * analogRead(therm[1].pin);
    float Vout3 = (5.0 / 1023.0) * analogRead(therm[2].pin);

    if (pwm_manuel != -1){
      envoyerPWM(pwm_manuel);
      Serial.println(pwm_manuel);


      if (modeCSV && t_s < DUREE_ENREGISTREMENT) {
        Serial.print(t_s, 3);
        Serial.print(","); Serial.print(T1, 2);
        Serial.print(","); Serial.print(T2, 2);
        Serial.print(","); Serial.print(T3, 2);
        Serial.print(","); Serial.print(T3, 2);
        Serial.print(","); Serial.print(T3, 2);
        Serial.print(","); Serial.print(T3, 2);
        Serial.print(","); Serial.print(0, 4);
        Serial.print(","); Serial.print(pwm_manuel);
        Serial.print(","); Serial.print(Vout1, 2);
        Serial.print(","); Serial.print(Vout2, 2);
        Serial.print(","); Serial.println(Vout3, 2);


      } else if (modeCSV) {
        Serial.println("FIN");
        modeCSV = false;
      }
    }
    else{

      float dT1 = T1 - T1_init;
      float dT2 = T2 - T2_init;

      float dT3_estimT1 = G1_b0 * dT1 + G1_b1 * u1_prev - G1_a1 * y1_prev;
      float T3_estimT1  = T3_init + dT3_estimT1;
      u1_prev = dT1;
      y1_prev = dT3_estimT1;

      float dT3_estimT2 = G2_b0 * dT2 + G2_b1 * u2_prev - G2_a1 * y2_prev;
      float T3_estimT2  = T3_init + dT3_estimT2;
      u2_prev = dT2;
      y2_prev = dT3_estimT2;

      float T3_moy = (T3_estimT1 + T3_estimT2) / 2.0;

      float a0 =  K * (1.0 + T_s / Ti + Td / T_s);
      float a1 =  -K * (1.0 + 2.0 * Td / T_s);
      float a2 =  K * (Td / T_s);
      Serial.println(a0);
      Serial.println(a1);
      Serial.println(a2);

      e[0] = setpoint - T3_moy;



      float u = u_prev + a0 * e[0] + a1 * e[1] + a2 * e[2];
      u_sat = constrain(u, U_MIN, U_MAX);


      envoyerPWM(u_sat);


      // On initialise les valeurs pour la prochaine itération
      u_prev = u;
      e[2] = e[1];
      e[1] = e[0];



    if (modeCSV && t_s < DUREE_ENREGISTREMENT) {
      Serial.print(t_s, 3);
      Serial.print(","); Serial.print(T1, 2);
      Serial.print(","); Serial.print(T2, 2);
      Serial.print(","); Serial.print(T3, 2);
      Serial.print(","); Serial.print(T3_estimT2, 2);
      Serial.print(","); Serial.print(T3_estimT1, 2);
      Serial.print(","); Serial.print(T3_moy, 2);
      Serial.print(","); Serial.print(e[0], 4);
      Serial.print(","); Serial.println(u_sat, 2);

    } else if (modeCSV) {
      Serial.println("FIN");
      modeCSV = false;
      }
    }
  }
}

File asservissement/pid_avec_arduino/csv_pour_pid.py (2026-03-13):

import serial
import csv
from datetime import datetime
import time
import os
import matplotlib.pyplot as plt
import pandas as pd

# ============ CONFIGURATION ============
PORT = 'COM6'
BAUDRATE = 9600

CHEMIN_ENREGISTREMENT = r'C:\Users\sabri\OneDrive\Desktop\uni\design\simulateur-thermique\asservissement\pid_avec_arduino\pid_avec_nouvelle_ident'

NOM_FICHIER = f'temperature_{datetime.now().strftime("%Y%m%d_%H%M%S")}.csv'
FICHIER_COMPLET = os.path.join(CHEMIN_ENREGISTREMENT, NOM_FICHIER)
# =======================================

# Crée le dossier si inexistant
os.makedirs(CHEMIN_ENREGISTREMENT, exist_ok=True)

print(f"Connexion au port {PORT}...")
ser = serial.Serial(PORT, BAUDRATE, timeout=1)
time.sleep(2)

print(f"Enregistrement dans :\n{FICHIER_COMPLET}\n")
print("Appuyez sur Ctrl+C pour arrêter\n")

entete_ecrit = False

with open(FICHIER_COMPLET, 'w', newline='', encoding='utf-8') as fichier:
    writer = csv.writer(fichier)

    try:
        while True:
            if ser.in_waiting > 0:
                ligne = ser.readline().decode('utf-8').strip()

                if ligne:
                    print(ligne)

                    if ligne == "FIN":
                        print("\n✓ Enregistrement terminé!")
                        break

                    if '\t' in ligne:
                        continue

                    # 9 colonnes
                    if ligne.count(',') == 8:
                        parties = ligne.split(',')

                        if len(parties) == 9 and all(p.strip() for p in parties):
                            try:
                                [float(p) for p in parties]
                                writer.writerow(parties)
                                fichier.flush()
                            except ValueError:
                                if not entete_ecrit:
                                    writer.writerow(parties)
                                    fichier.flush()
                                    entete_ecrit = True

    except KeyboardInterrupt:
        print("\n\n⚠ Arrêt manuel")
    finally:
        ser.close()
        print(f"\n✓ Fichier sauvegardé dans :\n{FICHIER_COMPLET}")

# ============ TRACÉ DU GRAPHIQUE ============
print("\nGénération du graphique...")

try:
    data = pd.read_csv(FICHIER_COMPLET, header=None,
                       names=['temps_s', 'T1_C', 'T2_C', 'T3_C',
                              'T3_estimT2', 'T3_estimT1', 'T3_moy',
                              'erreur', 'commande_u'])
    data = data[pd.to_numeric(data['temps_s'], errors='coerce').notna()].astype(float).reset_index(drop=True)

    if len(data) == 0:
        print("❌ Aucune donnée à tracer!")
    else:
        print(f"✓ {len(data)} lignes chargées")

        fig, axes = plt.subplots(3, 1, figsize=(14, 12), sharex=True)
        fig.suptitle('Contrôleur PID — T3 estimée', fontsize=14, fontweight='bold')

        # ── Graphique 1 : T3 mesurée, estimée, setpoint ──
        axes[0].plot(data['temps_s'], data['T3_C'],
                     color='#2196F3', linewidth=1.5, label='T3 mesurée')
        axes[0].plot(data['temps_s'], data['T3_moy'],
                     color='#4CAF50', linewidth=1.5, linestyle='--', label='T3_moy (estimée)')
        axes[0].axhline(y=30.0, color='#F44336', linestyle='--',
                        linewidth=1.2, label='Consigne (30°C)')
        axes[0].set_ylabel('Température (°C)')
        axes[0].set_title('T3 mesurée vs T3 estimée moyenne')
        axes[0].legend(fontsize=10)
        axes[0].grid(True, alpha=0.3)

        # ── Graphique 2 : Erreur ──
        axes[1].plot(data['temps_s'], data['erreur'],
                     color='#9C27B0', linewidth=1.5, label='Erreur')
        axes[1].axhline(y=0, color='black', linestyle='--', linewidth=0.8)
        axes[1].fill_between(data['temps_s'], data['erreur'], 0,
                             where=(data['erreur'] > 0), alpha=0.15,
                             color='#F44336', label='Trop froid')
        axes[1].fill_between(data['temps_s'], data['erreur'], 0,
                             where=(data['erreur'] < 0), alpha=0.15,
                             color='#2196F3', label='Trop chaud')
        axes[1].set_ylabel('Erreur (°C)')
        axes[1].set_title('Erreur du PID')
        axes[1].legend(fontsize=10)
        axes[1].grid(True, alpha=0.3)

        # ── Graphique 3 : Commande u ──
        axes[2].plot(data['temps_s'], data['commande_u'],
                     color='#FF9800', linewidth=1.5, label='Commande u')
        axes[2].axhline(y= 255, color='#F44336', linestyle=':', linewidth=0.8, label='Sat. +255')
        axes[2].axhline(y=-255, color='#2196F3', linestyle=':', linewidth=0.8, label='Sat. -255')
        axes[2].axhline(y=0,    color='black',   linestyle='-',  linewidth=0.8)
        axes[2].fill_between(data['temps_s'], data['commande_u'], 0,
                             where=(data['commande_u'] > 0), alpha=0.12, color='#F44336')
        axes[2].fill_between(data['temps_s'], data['commande_u'], 0,
                             where=(data['commande_u'] < 0), alpha=0.12, color='#2196F3')
        axes[2].set_ylabel('Commande u (PWM)')
        axes[2].set_xlabel('Temps (s)')
        axes[2].set_title('Commande PWM appliquée')
        axes[2].set_ylim(-270, 270)
        axes[2].legend(fontsize=10)
        axes[2].grid(True, alpha=0.3)

        plt.tight_layout()

        nom_image = FICHIER_COMPLET.replace('.csv', '_PID.png')
        plt.savefig(nom_image, dpi=300, bbox_inches='tight')
        print(f"✓ Graphique sauvegardé : {nom_image}")
        plt.show()

        print("\n✓ Terminé!")

except Exception as e:
    print(f"\n❌ Erreur lors de la génération du graphique : {e}")
    print("Vérifiez le contenu du fichier CSV.")

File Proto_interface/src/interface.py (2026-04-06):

import tkinter as tk
from tkinter import messagebox
from matplotlib.backends.backend_tkagg import FigureCanvasTkAgg
import serial
import time
import datetime
import pandas as pd
import serial.tools.list_ports
from tkinter import filedialog
from matplotlib.figure import Figure


class InterfaceProto:
    def __init__(self, root):
        self.root = root
        self.root.title("Contrôle du prototype")

        self.ser = None
        self.running = False
        self.start_time = None

        # timer
        self.timer_start = None
        self.duree_cible = 300
        self.timer_termine = False

        # temp
        self.temperature_voulue = 30
        self.temperature_ambiante = 23.5
        self.temperature_initiale = self.temperature_ambiante
        self.applied = False

        # pid réchauffement
        self.kp_chaud = 9.2
        self.ti_chaud = 250
        self.td_chaud = 35

        # pid refroidissement
        self.kp_froid = 10.5
        self.ti_froid = 230
        self.td_froid = 40

        self.times = []
        self.t1_data = []
        self.t2_data = []
        self.t3est_data = []
        self.u_data = []
        self.e_data = []
        self.t3reel_data = []
        self.consigne = []

        self.create_widgets()

    def create_widgets(self):
        BG = "#F5EFF3"
        CARD = "#FFFFFF"
        SURFACE = "#F5EFF3"
        WINE = "#4B0E26"
        MUTED = "#7A5568"
        TEXT = "#1A0A10"
        BORDER = "#D9C8D4"


        self.root.configure(bg=BG)

        outer = tk.Frame(self.root, bg=BG)
        outer.pack(fill="both", expand=True, padx=14, pady=10)

        # ── En-tête ───────────────────────────────────────────────────
        header = tk.Frame(outer, bg=CARD, highlightthickness=1,
                          highlightbackground=BORDER)
        header.pack(fill="x", pady=(0, 6))

        left_h = tk.Frame(header, bg=CARD)
        left_h.pack(side="left", padx=12, pady=6)

        dot = tk.Canvas(left_h, width=20, height=20, bg=CARD,
                        highlightthickness=0)
        dot.create_oval(0, 0, 20, 20, fill=WINE, outline="")
        dot.pack(side="left", padx=(0, 8))

        tk.Label(left_h, text="Contrôleur PID — Prototype thermique — Équipe 5",
                 font=("Arial", 12, "bold"), bg=CARD, fg=TEXT).pack(side="left")

        right_h = tk.Frame(header, bg=CARD)
        right_h.pack(side="right", padx=12)
        self.status_label = tk.Label(
            right_h, text="● En attente",
            font=("Courier", 10), bg="#EAF3DE", fg="#3B6D11",
            relief="flat", padx=8, pady=3
        )
        self.status_label.pack()

        # ── Boutons d'action ──────────────────────────────────────────
        btn_row = tk.Frame(outer, bg=BG)
        btn_row.pack(fill="x", pady=(0, 6))
        for i in range(4):
            btn_row.grid_columnconfigure(i, weight=1, uniform="btn")

        btns = [
            ("Démarrer le prototype", "#174D1C", "#E8F5EA", self.demarrer_proto),
            ("Arrêter le prototype", "#832828", "#FAE8E8", self.arreter_proto),
            ("Ramener à température ambiante", WINE, "#F9EFF4", self.ramener_ambiante),
            ("Enregistrer les données", "#1A3A5C", "#E6F1FB", self.enregistrer_donnees),
        ]
        for i, (txt, bg, fg, cmd) in enumerate(btns):
            tk.Button(
                btn_row, text=txt, command=cmd,
                font=("Arial", 12, "bold"), bg=bg, fg=fg,
                relief="flat", pady=9, cursor="hand2",
                activebackground=bg, activeforeground=fg
            ).grid(row=0, column=i, padx=4, sticky="ew")

        # ── Métriques temps réel ──────────────────────────────────────────────
        metrics_row = tk.Frame(outer, bg=BG)
        metrics_row.pack(fill="x", pady=(0, 6))
        for i in range(5):
            metrics_row.grid_columnconfigure(i, weight=1, uniform="metric")

        metric_defs = [
            ("T1 — Thermistance 1", "metric_t1"),
            ("T2 — Thermistance 2", "metric_t2"),
            ("T3 — Estimée", "metric_t3"),
            ("Erreur courante", "metric_err"),
            ("Commande (PWM)", "metric_u"),
        ]
        for i, (lbl, attr) in enumerate(metric_defs):
            card = tk.Frame(metrics_row, bg=CARD, highlightthickness=1,
                            highlightbackground=BORDER)
            card.grid(row=0, column=i, padx=4, sticky="nsew")
            tk.Label(card, text=lbl, font=("Arial", 10), bg=CARD,
                     fg=MUTED).pack(anchor="w", padx=10, pady=(6, 0))
            var = tk.StringVar(value="— °C" if "metric_t" in attr or attr == "metric_err" else "—")
            tk.Label(card, textvariable=var,
                     font=("Courier", 16, "bold"), bg=CARD,
                     fg=TEXT).pack(anchor="w", padx=10, pady=(1, 6))
            setattr(self, attr, var)
        # ── Corps ─────────────────────────────────────────────────────────────
        body = tk.Frame(outer, bg=BG)
        body.pack(fill="both", expand=True)
        body.grid_columnconfigure(0, weight=0, minsize=290)
        body.grid_columnconfigure(1, weight=1)
        body.grid_rowconfigure(0, weight=1)

        # ── Colonne gauche ────────────────────────────────────────────────────
        left_col = tk.Frame(body, bg=BG)
        left_col.grid(row=0, column=0, sticky="ns", padx=(0, 10))

        def section_title(parent, text):
            f = tk.Frame(parent, bg=BG)
            f.pack(fill="x", pady=(5, 2))
            tk.Frame(f, bg=WINE, width=3, height=12).pack(side="left",
                                                          padx=(0, 5))
            tk.Label(f, text=text.upper(), font=("Arial", 9, "bold"),
                     bg=BG, fg=WINE).pack(side="left")

        # Carte réglages
        section_title(left_col, "Réglages")
        reglages_card = tk.Frame(left_col, bg=CARD, highlightthickness=1,
                                 highlightbackground=BORDER)
        reglages_card.pack(fill="x", pady=(0, 8))

        inner = tk.Frame(reglages_card, bg=CARD)
        inner.pack(fill="x", padx=12, pady=10)
        inner.grid_columnconfigure(0, weight=1)
        inner.grid_columnconfigure(1, weight=0)

        # Température cible
        tk.Label(inner, text="Température à atteindre (°C) :",
                 font=("Arial", 11), bg=CARD, fg=MUTED) \
            .grid(row=0, column=0, sticky="w", pady=(0, 6))
        self.temperature_entry_att = tk.Entry(
            inner, width=7, font=("Courier", 12),
            bg=SURFACE, fg=TEXT, relief="flat",
            highlightthickness=1, highlightbackground=BORDER, justify="right"
        )
        self.temperature_entry_att.insert(0, self.temperature_voulue)
        self.temperature_entry_att.grid(row=0, column=1, pady=(0, 6))
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

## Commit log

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2026-02-04 ajout kicad
    [circuit_thermistances.kicad_pcb, circuit_thermistances.kicad_sch]
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2026-02-04 Graphique du csv fonctionnel
    [temperature_20260204_134655.csv, temperature_20260204_135910.csv]
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2026-02-04 identification thermistances!
    [25_35.csv, 25_45.csv, 35_35.csv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]
2026-02-05 debut pcb
    [Arduino_MEGA_2560-Rev3-2026-02-04-22-12-31.sch, Arduino_MEGA_2560-Rev3.kicad_pcb, Arduino_MEGA_2560-Rev3.kicad_sch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]
2026-02-06 procrastination pendant optique
    [pcb.csv, pcb.kicad_pcb, pcb.kicad_sch]
2026-02-08 pcb yaddi yadda
    [pcb.kicad_pcb, pcb.kicad_sch]
2026-02-09 version tht pour pas trop haïr notre vie plus tard
    [pcb.kicad_pcb, pcb.kicad_sch]
2026-02-09 Changment connecteur pcb
    [freerouting.dsn, pcb.kicad_pcb, pcb.kicad_sch]
2026-02-09 Pcb quasi fini
    [pcb.kicad_pcb, pcb.kicad_sch]
2026-02-09 PCB + BOM
    [freerouting.dsn, pcb.kicad_pcb]
2026-02-10 PCB partie 4, bom fini ?
    [pcb.csv, pcb.kicad_sch]
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2026-02-10 Changements connecteurs
    [pcb-B_Silkscreen.gbr, pcb-Bottom.gbr, pcb-Edge_Cuts.gbr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]
2026-02-10 PC V2 fini
    [pcb.kicad_pcb, pcb.kicad_sch]
2026-02-11 Commit Vmille
    [pcb.kicad_pcb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]
2026-02-11 PCB V2 - Envoyé à Martin
    [pcb.kicad_pcb, pcb.kicad_sch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]
2026-02-11 planif achat pcb
    [Achats composants.xlsx, pcb.kicad_pcb]
2026-02-11 graph 3 thermistances
    [10_30_t1.csv, 10_30_t2.csv, 35_55.t1.csv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]
2026-02-12 données
    [10_30_t1.csv]
2026-02-15 Modifs valeur R schematic
    [pcb.kicad_pcb, pcb.kicad_sch]
2026-02-16 lecture 3 thermistances
    [10_30_t1.csv, resultats_simulation.csv]
2026-02-16 h trouvé yééééé
    [temperature_20260216_172323.csv]
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2026-02-25 esti de kicad
    [pcb.kicad_sch]
2026-02-27 PCB V2
    [D0008A.stp, LMC6482IMX_NOPB.step, c-640445-2-al-3d.stp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]
2026-02-27 Gerber files exportés, on commande?
    [pcb-B_Adhesive.gbr, pcb-B_Courtyard.gbr, pcb-B_Fab.gbr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]
2026-02-28 V4 zip file
    [pcb-B_Adhesive.gbr, pcb-B_Courtyard.gbr, pcb-B_Fab.gbr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]
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2026-03-05 asservissement avec arduino test du code avec une consigne de 28, une perturbation qui rechauffe, une perturbation qui refroidit
    [consigne28_perturbations.csv]
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2026-03-09 timer correction
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2026-03-09 Sauvegardes mineurs kicad et BOM
    [bom2.csv]
2026-03-10 génération de graphique après asservissement
    [testpi_10.csv]
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2026-03-13 gros update asservissement: - changement d'endroit de certains fichiers - identification des trois thermistances en chauffant/refroidissant avec petite/grande commande (à retester avec commande de 30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
    [Tconstante.csv, c0_froid.csv, c10_chaud.csv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]
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2026-03-17 données de lundi
    [temperature_20260316_151707.csv, temperature_20260316_154735.csv, temperature_20260316_155239.csv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]
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2026-03-19 test interface
    [temperature_20260319_125143.csv, temperature_20260319_130357.csv]
2026-03-19 test pour reset graphiques interface proto
    [interface.py]
2026-03-19 test pour reset graphiques interface proto 2
    [interface.py]
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2026-03-20 Fichier Arduino qui fonctionne bien, on a changé: - u_prev = u quand pas saturé - reset des u_prev et e[1], e[2] quand on applique une nouvelle configuration. On lit pas les bonnes températures des t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
    On print les lignes de l'Arduino dans le terminal aussi! En mode débogage :o
    [interface.py, main.cpp]
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2026-03-21 modification du main pour reset le temps écoulé à 0 quand on applique une nouvelle commande
    [main.cpp]
2026-03-22 correction consigne enregistrement des donnees
    [interface.py]
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2026-03-23 impression schéma électrique pour éval prototype
    [pcb.kicad_sch]
2026-03-23 excel (ugh)
    [2023.csv]
2026-03-24 evaluation prototype
    [Tests_Proto_H26_Equipe05.xlsx]
2026-03-29 validation et résultats du simulateur
    [simulation5.csv]
2026-04-01 enregistrement pu de bug
    [interface.py]
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2026-04-01 SIMULINK QUI MARCHE
    [simulationchat.csv]
2026-04-01 prise des mesures pour le prototype en boucle ouverte (rapport 3)
    [-10pwm_depuis21.csv, -20pwm_depuis22.csv, -40pwm_depuis31.csv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]
2026-04-03 ajout interface simulinl
    [comparaison.csv, donnees.csv, donnees2330.csv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]
2026-04-03 amélioration simulink - interface (clicker sur apply, puis lance la simulation, pour voir blocs, clicker sur petite flêche en bas à gauche du mask) - possibilité de modification des paramètres - enre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
    Reste à faire:
    - nouvelle ident pour refroidissement aussi
    - ajout de perturbations
    - faire une ident pour procédé excepté thermistance, puis ensuite décomposé la thermistance avec la formule
    [simulation.csv]
2026-04-03 régalge bug lors du changement des dimensions de la plaque dans la simulation thermique
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2026-04-05 graphique pour identifier la puissance en chauffage et en refroidissement avec les nouvelles données
    [-40pwm_depuis31.csv, 20pwm_depuis21.csv]
2026-04-06 prise de données
    [10pwm_depuis20.csv, 10pwm_depuis25.csv, 10pwm_depuis28.csv]
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2026-04-07 données + calculs puissance
    [-10pwm_depuis22.csv, -10pwm_depuis24.csv, -10pwm_depuis26.csv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]
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2026-04-09 boucle ouverte simulink proto
    [Boucle_ouverte.xlsx]
2026-04-09 modifs simulink: - pid dans interface - perturbation (à voir au mettre) - saturation
    [simulation.csv]
2026-04-09 Boucle ouverte V2
    [-10pwm_depuis23.csv, 20pwm_depuis24.csv]
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2026-04-09 graphiques boucleouverte
    [Boucle_ouverte.xlsx]
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2026-04-09 code+graphique boucle ouverte / ferme / perturbation
    [-10pwm_depuis22.csv, -10pwm_depuis23.csv, -10pwm_depuis24.csv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]
2026-04-09 proto BF
    [24.5_30_sans_perturb.csv, 25_35_sans_perturb.csv]
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2026-04-09 graphs_bo_changement de nom
    $$$$
    [-10pwm_depuis23_bo.csv, -20pwm_depuis22_bo.csv, -40pwm_depuis31_bo.csv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]
2026-04-09 BF avec pertrbations fini 9 avril
    [24_16_perturb_30s.csv, 24_28_perturb_100s.csv, 24_30_perturb_30s.csv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]
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2026-04-09 boucle fermee sans perturbation
    [Boucle_fermee_sans_perturb.xlsx]
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
